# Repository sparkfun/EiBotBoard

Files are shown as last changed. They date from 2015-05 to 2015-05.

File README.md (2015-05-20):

EiBotBoard
==========
EiBotBoard

[*EiBotBoard (WIG-10025)*](https://www.sparkfun.com/products/10025)

The EiBotBoard (EBB) was originally designed for the Egg-Bot project. 
It is a small (2.2" x 2.2") two channel stepper motor driver board with USB microcontroller. 
It is based on the UBW board and supports all of the commands that the UBW does (for the most part), plus several extra, like stepper motor commands and RC servo output commands.

Repository Contents
-------------------
* **/Hardware** - All Eagle design files (.brd, .sch)
* **/Production** - Production panel files (.brd)

License Information
-------------------
Distributed as-is; no warranty is given.

_**Note:** This product is a collaboration with Brian Schmalz. A portion of each sales goes back to him for product support and continued development._

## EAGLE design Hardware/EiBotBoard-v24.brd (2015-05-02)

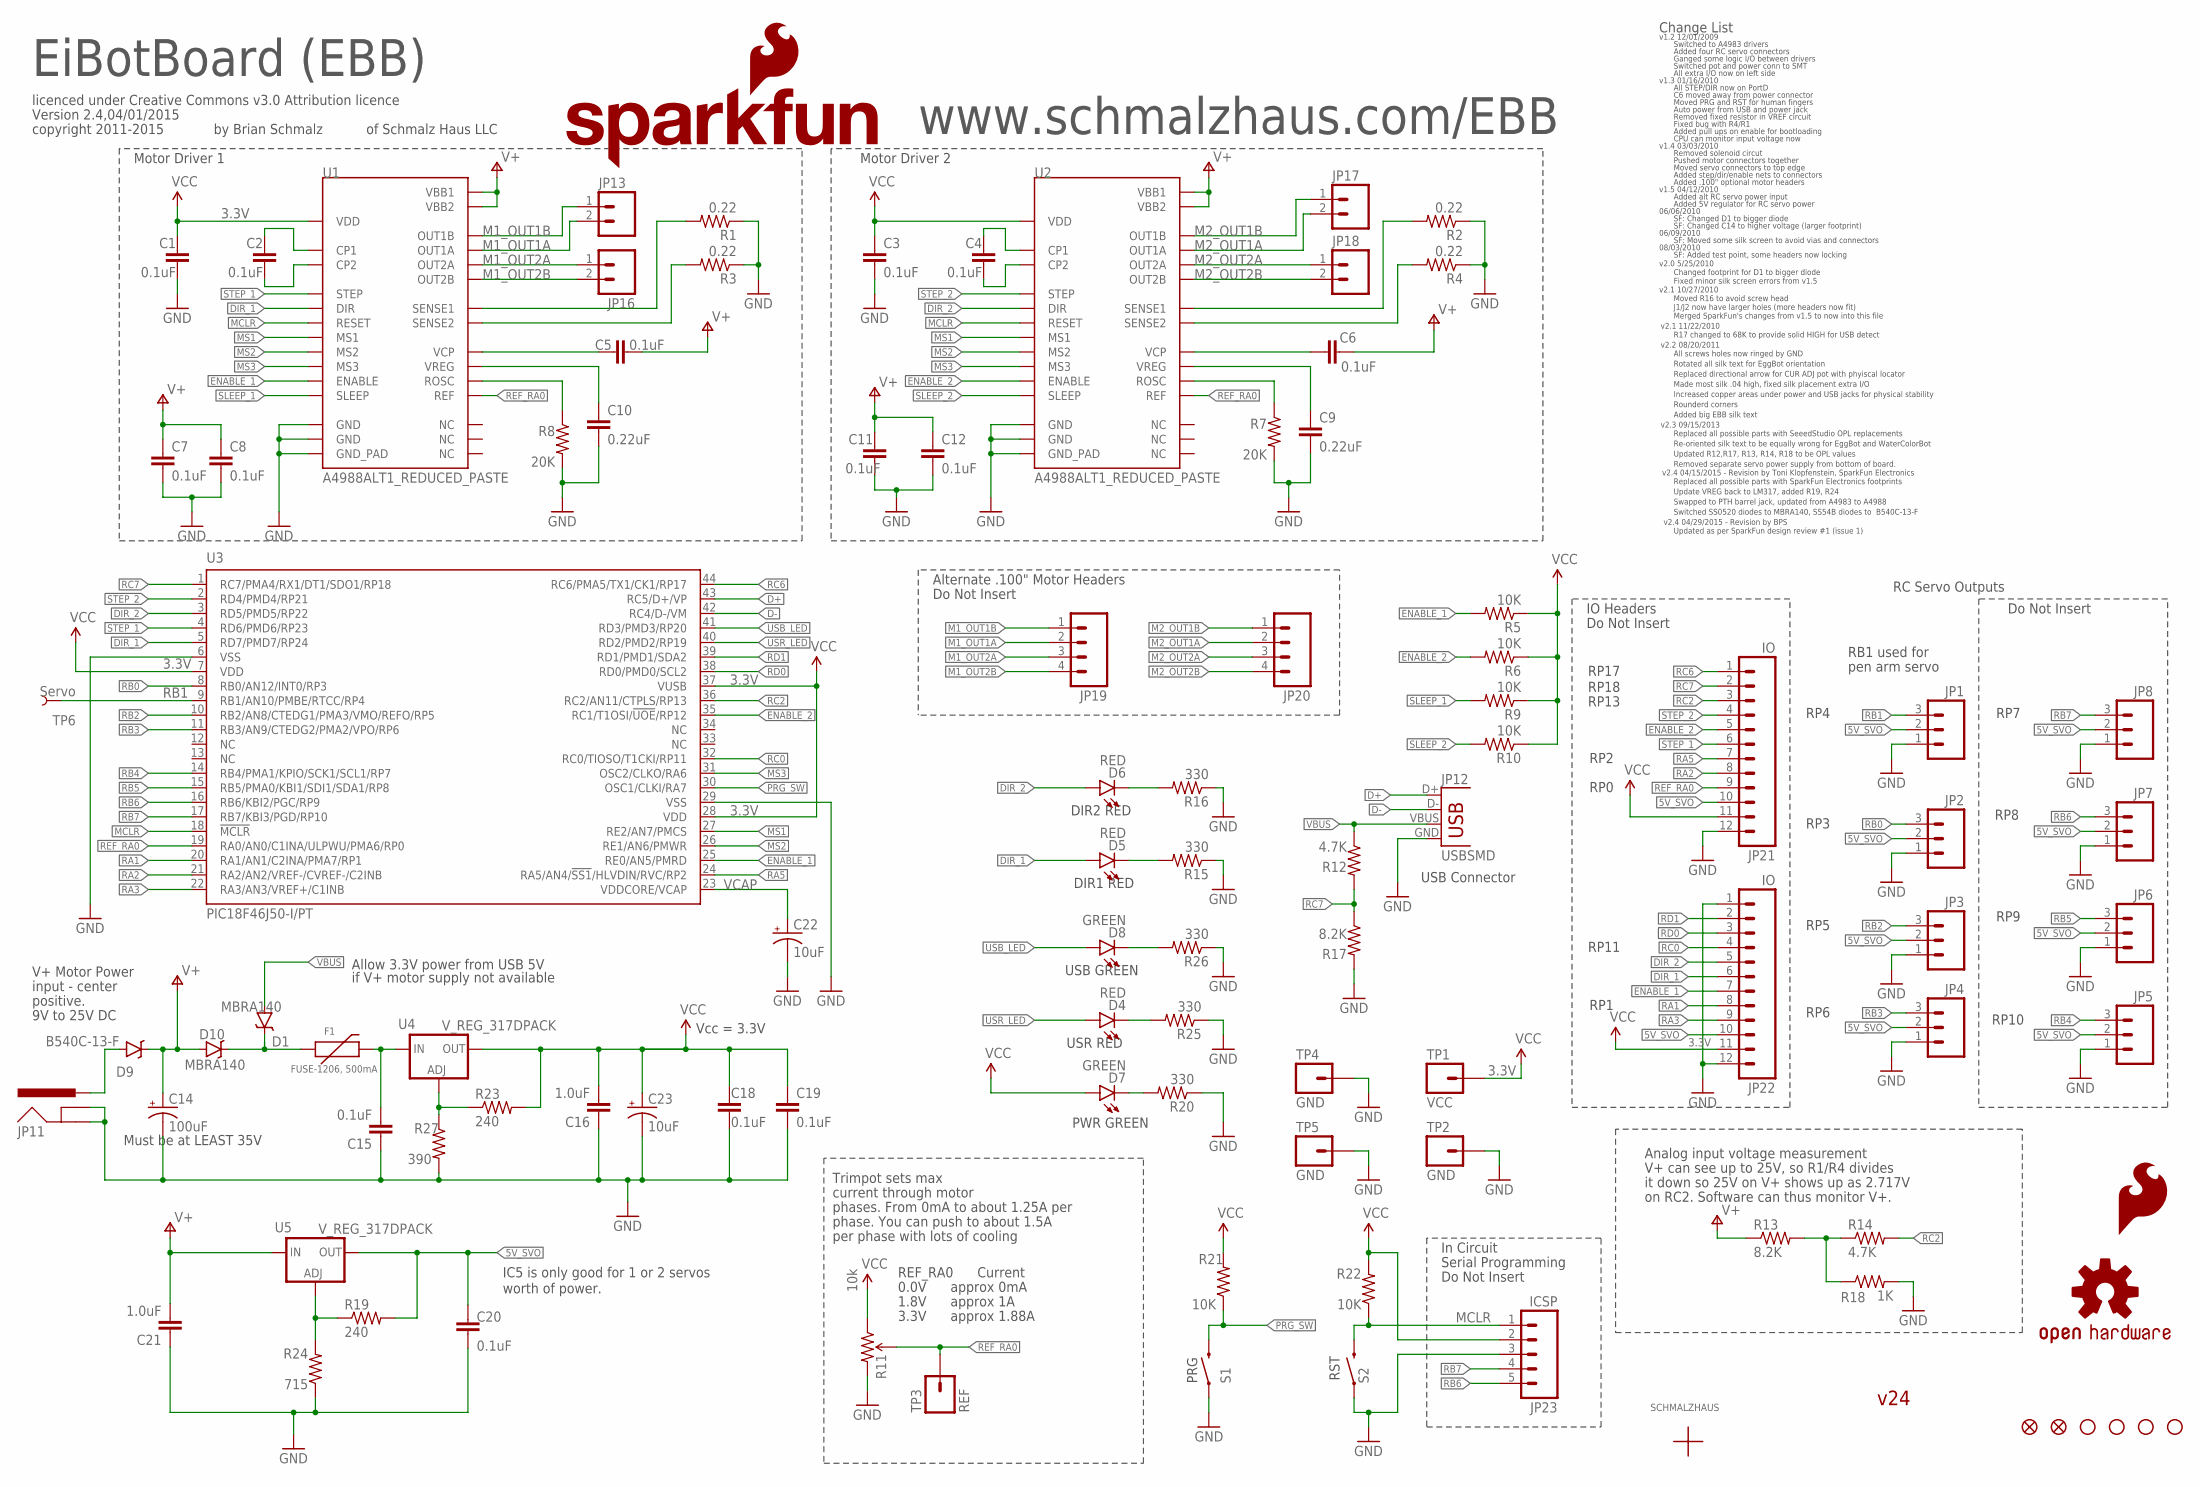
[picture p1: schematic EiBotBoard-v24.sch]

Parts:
C1, C2, C3, C4, C5, C6, C7, C8, C11, C12, C15, C18, C19, C20: 0.1uF; 0603-CAP
C9, C10: 0.22uF; 0603-CAP
C14: 100uF; NIC_10X10.5_CAP
C16, C21: 1.0uF; 0603-CAP
C22, C23: 10uF; EIA3528
D1, D10: MBRA140; SMA-DIODE
D4, D5, D6: RED; LED-0603
D7, D8: GREEN; LED-0603
D9: B540C-13-F; SMC
F1: FUSE-1206, 500mA; PTC-1206
JP1, JP2, JP3, JP4, JP5, JP6, JP7, JP8: M03LOCK_NO_SILK; 1X03_LOCK_NO_SILK
JP11: POWER_JACKPTH_LOCK; POWER_JACK_PTH_LOCK
JP12: USBSMD; USB-MINIB
JP13, JP16, JP17, JP18: M023.5MM_LOCK; SCREWTERMINAL-3.5MM-2_LOCK
JP14, JP15: FIDUCIAL1X2; FIDUCIAL-1X2
JP19, JP20: M04POLAR; MOLEX-1X4
JP21, JP22: IO; 1X12
JP23: ICSP; 1X05_NO_SILK
LOGO1: OSHW-LOGOS; OSHW-LOGO-S
LOGO2: SFE_LOGO_FLAME.2_INCH; SFE_LOGO_FLAME_.2
LOGO3: SFE_LOGO_NAME_FLAME.2_INCH; SFE_LOGO_NAME_FLAME_.2
R1, R2, R3, R4: 0.22; 0805
R5, R6, R9, R10, R21, R22: 10K; 0603-RES
R7, R8: 20K; 0603-RES
R11: 10k; TRIMPOT-3MM
R12, R14: 4.7K; 0603-RES
R13, R17: 8.2K; 0603-RES
R15, R16, R20, R25, R26: 330; 0603-RES
R18: 1K; 0603-RES
R19, R23: 240; 0603-RES
R24: 715; 0603-RES
R27: 390; 0603-RES
S1, S2: SWITCH-MOMENTARY-2SMD; TACTILE-SWITCH-SMD
TP1: VCC; 1X01_NOSILK
TP2, TP4, TP5: GND; 1X01_NOSILK
TP3: REF; 1X01
TP6: Servo; PAD.03X.05
U1, U2: A4988ALT1_REDUCED_PASTE; QFN-28-5MM_ALT1_REDUCED_PASTE
U3: PIC18F46J50-I/PT; TQFP44
U4, U5: V_REG_317DPACK; V-REG_DPACK
U$1: SCHMALZHAUSSCHMALZHAUS_SMALL; SCHMALZHAUS_SMALL
U$2, U$3, U$4, U$5: STAND-OFF

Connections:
3.3V: C1.1, C3.1, C16.2, C18.2, C19.2, C23.A (+), D7.A, JP21.11, JP22.11, JP23.2, R5.1, R6.1, R9.1, R10.1, R11.1 (CCW), R21.2, R22.2, R23.2, TP1.1, U1.P$15 (VDD), U2.P$15 (VDD), U3.7 (VDD), U3.28 (VDD), U3.37 (VUSB), U4.4 (OUT)
5V_SVO: C20.2, JP1.2, JP2.2, JP3.2, JP4.2, JP5.2, JP6.2, JP7.2, JP8.2, JP21.10, JP22.10, R19.2, U5.4 (OUT)
D+: JP12.D+, U3.43 (RC5/D+/VP)
D-: JP12.D-, U3.42 (RC4/D-/VM)
DIR_1: D5.A, JP22.6, U1.P$19 (DIR), U3.5 (RD7/PMD7/RP24)
DIR_2: D6.A, JP22.5, U2.P$19 (DIR), U3.3 (RD5/PMD5/RP22)
ENABLE_1: JP22.7, R5.2, U1.P$2 (ENABLE), U3.25 (RE0/AN5/PMRD)
ENABLE_2: JP21.5, R6.2, U2.P$2 (ENABLE), U3.35 (RC1/T1OSI/!UOE!/RP12)
GND: C1.2, C3.2, C7.2, C8.2, C9.2, C10.2, C11.2, C12.2, C14.-, C15.1, C16.1, C18.1, C19.1, C20.1, C21.1, C22.C (-), C23.C (-), JP1.1, JP2.1, JP3.1, JP4.1, JP5.1, JP6.1, JP7.1, JP8.1, JP11.GND, JP11.GNDBREAK, JP12.GND, JP21.12, JP22.1, JP22.12, JP23.3, R1.1, R2.1, R3.1, R4.1, R7.2, R8.2, R11.3 (CW), R15.1, R16.1, R17.2, R18.2, R20.1, R24.1, R25.1, R26.1, R27.2, S1.1, S2.1, TP2.1, TP4.1, TP5.1, U1.P$3 (GND), U1.P$18 (GND), U1.P$29 (GND_PAD), U2.P$3 (GND), U2.P$18 (GND), U2.P$29 (GND_PAD), U3.6 (VSS), U3.29 (VSS)
M1_OUT1A: JP13.2, JP19.2, U1.P$24 (OUT1A)
M1_OUT1B: JP13.1, JP19.1, U1.P$21 (OUT1B)
M1_OUT2A: JP16.1, JP19.3, U1.P$26 (OUT2A)
M1_OUT2B: JP16.2, JP19.4, U1.P$1 (OUT2B)
M2_OUT1A: JP17.2, JP20.2, U2.P$24 (OUT1A)
M2_OUT1B: JP17.1, JP20.1, U2.P$21 (OUT1B)
M2_OUT2A: JP18.1, JP20.3, U2.P$26 (OUT2A)
M2_OUT2B: JP18.2, JP20.4, U2.P$1 (OUT2B)
MCLR: JP23.1, R22.1, S2.3 (2), U1.P$12 (RESET), U2.P$12 (RESET), U3.18 (!MCLR!)
MS1: U1.P$9 (MS1), U2.P$9 (MS1), U3.27 (RE2/AN7/PMCS)
MS2: U1.P$10 (MS2), U2.P$10 (MS2), U3.26 (RE1/AN6/PMWR)
MS3: U1.P$11 (MS3), U2.P$11 (MS3), U3.31 (OSC2/CLKO/RA6)
unnamed: D6.C, R16.2
unnamed: D1.C, D10.C, F1.1
unnamed: C2.1, U1.P$4 (CP1)
unnamed: R13.2, R14.1, R18.1
unnamed: C2.2, U1.P$5 (CP2)
unnamed: D9.A, JP11.PWR
unnamed: D5.C, R15.2
unnamed: D8.C, R26.2
unnamed: R23.1, R27.1, U4.1 (ADJ)
unnamed: D4.C, R25.2
unnamed: D7.C, R20.2
unnamed: R19.1, R24.2, U5.1 (ADJ)
unnamed: C4.1, U2.P$4 (CP1)
unnamed: C4.2, U2.P$5 (CP2)
unnamed: R8.1, U1.P$13 (ROSC)
unnamed: C10.1, U1.P$8 (VREG)
unnamed: C5.1, U1.P$6 (VCP)
unnamed: R3.2, U1.P$27 (SENSE2)
unnamed: R1.2, U1.P$23 (SENSE1)
unnamed: C15.2, F1.2, U4.3 (IN)
unnamed: C6.1, U2.P$6 (VCP)
unnamed: R2.2, U2.P$23 (SENSE1)
unnamed: R4.2, U2.P$27 (SENSE2)
unnamed: C9.1, U2.P$8 (VREG)
unnamed: R7.1, U2.P$13 (ROSC)
PRG_SW: R21.1, S1.3 (2), U3.30 (OSC1/CLKI/RA7)
RA1: JP22.8, U3.20 (RA1/AN1/C2INA/PMA7/RP1)
RA2: JP21.8, U3.21 (RA2/AN2/VREF-/CVREF-/C2INB)
RA3: JP22.9, U3.22 (RA3/AN3/VREF+/C1INB)
RA5: JP21.7, U3.24 (RA5/AN4/!SS1!/HLVDIN/RVC/RP2)
RB0: JP2.3, U3.8 (RB0/AN12/INT0/RP3)
RB1: JP1.3, TP6.P$1, U3.9 (RB1/AN10/PMBE/RTCC/RP4)
RB2: JP3.3, U3.10 (RB2/AN8/CTEDG1/PMA3/VMO/REFO/RP5)
RB3: JP4.3, U3.11 (RB3/AN9/CTEDG2/PMA2/VPO/RP6)
RB4: JP5.3, U3.14 (RB4/PMA1/KPIO/SCK1/SCL1/RP7)
RB5: JP6.3, U3.15 (RB5/PMA0/KBI1/SDI1/SDA1/RP8)
RB6: JP7.3, JP23.5, U3.16 (RB6/KBI2/PGC/RP9)
RB7: JP8.3, JP23.4, U3.17 (RB7/KBI3/PGD/RP10)
RC0: JP22.4, U3.32 (RC0/TIOSO/T1CKI/RP11)
RC2: JP21.3, R14.2, U3.36 (RC2/AN11/CTPLS/RP13)
RC6: JP21.1, U3.44 (RC6/PMA5/TX1/CK1/RP17)
RC7: JP21.2, R12.2, R17.1, U3.1 (RC7/PMA4/RX1/DT1/SDO1/RP18)
RD0: JP22.3, U3.38 (RD0/PMD0/SCL2)
RD1: JP22.2, U3.39 (RD1/PMD1/SDA2)
REF_RA0: JP21.9, R11.2 (WIPER), TP3.1, U1.P$17 (REF), U2.P$17 (REF), U3.19 (RA0/AN0/C1INA/ULPWU/PMA6/RP0)
SLEEP_1: R9.2, U1.P$14 (SLEEP)
SLEEP_2: R10.2, U2.P$14 (SLEEP)
STEP_1: JP21.6, U1.P$16 (STEP), U3.4 (RD6/PMD6/RP23)
STEP_2: JP21.4, U2.P$16 (STEP), U3.2 (RD4/PMD4/RP21)
USB_LED: D8.A, U3.41 (RD3/PMD3/RP20)
USR_LED: D4.A, U3.40 (RD2/PMD2/RP19)
V+: C5.2, C6.2, C7.1, C8.1, C11.1, C12.1, C14.+, C21.2, D9.C, D10.A, R13.1, U1.P$22 (VBB1), U1.P$28 (VBB2), U2.P$22 (VBB1), U2.P$28 (VBB2), U5.3 (IN)
VBUS: D1.A, JP12.VBUS, R12.1
VCAP: C22.A (+), U3.23 (VDDCORE/VCAP)

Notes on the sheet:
EiBotBoard (EBB)
v1.2 12/01/2009
by Brian Schmalz
of Schmalz Haus LLC
www.schmalzhaus.com/EBB
licenced under Creative Commons v3.0 Attribution licence
PWR GREEN
DIR1 RED
DIR2 RED
USR RED
USB GREEN
PRG
RST
RP17
RP18
Change List
Switched to A4983 drivers
Added four RC servo connectors
Ganged some logic I/O between drivers
Switched pot and power conn to SMT
All extra I/O now on left side
Vcc = 3.3V
v1.3 01/16/2010
All STEP/DIR now on PortD
C6 moved away from power connector
Moved PRG and RST for human fingers
Auto power from USB and power jack
Removed fixed resistor in VREF circuit
Fixed bug with R4/R1
CPU can monitor input voltage now
Added pull ups on enable for bootloading
V+ can see up to 25V, so R1/R4 divides
it down so 25V on V+ shows up as 2.717V
Analog input voltage measurement
on RC2. Software can thus monitor V+.
RP11
Version 2.4,04/01/2015
v1.4 03/03/2010
Removed solenoid circut
Pushed motor connectors together

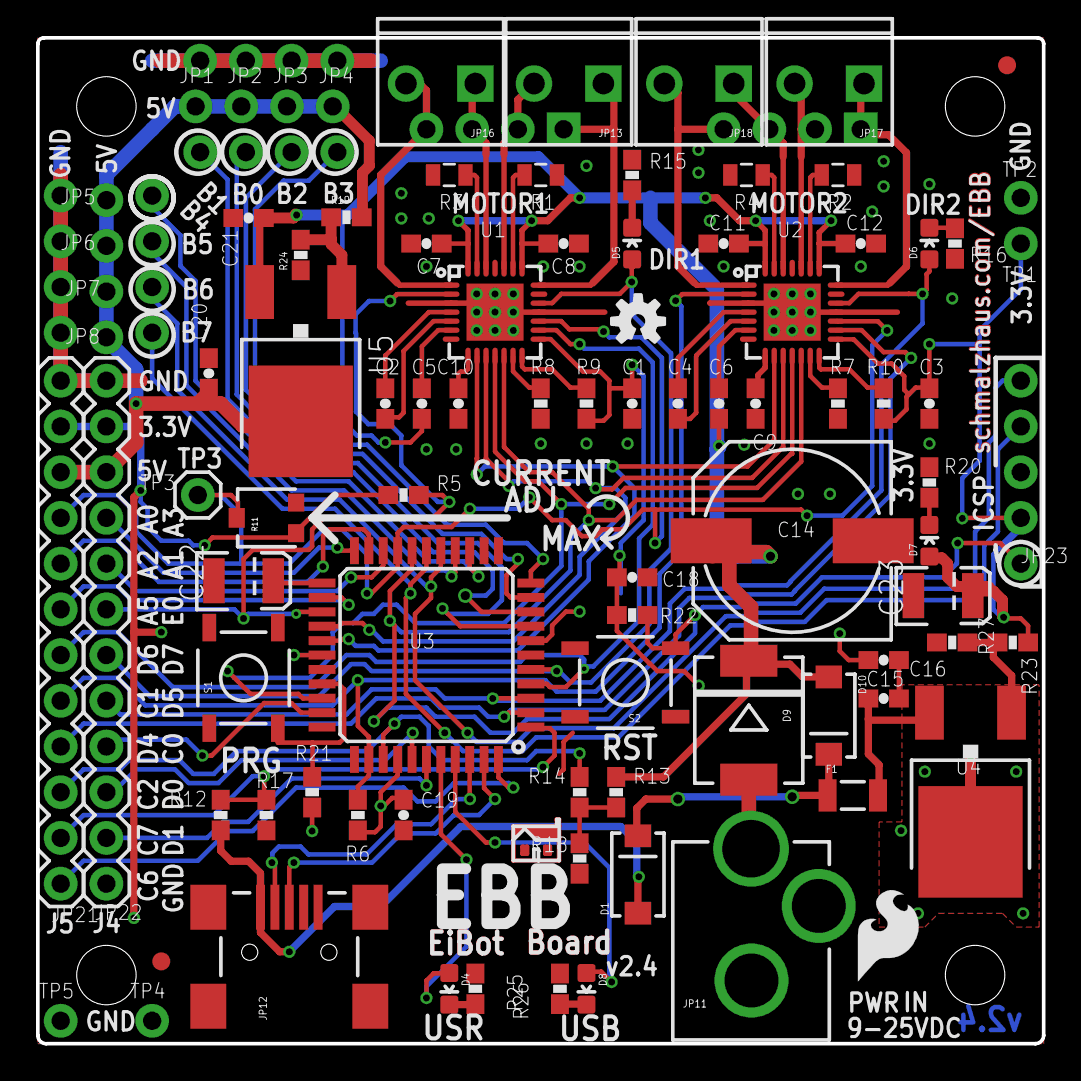
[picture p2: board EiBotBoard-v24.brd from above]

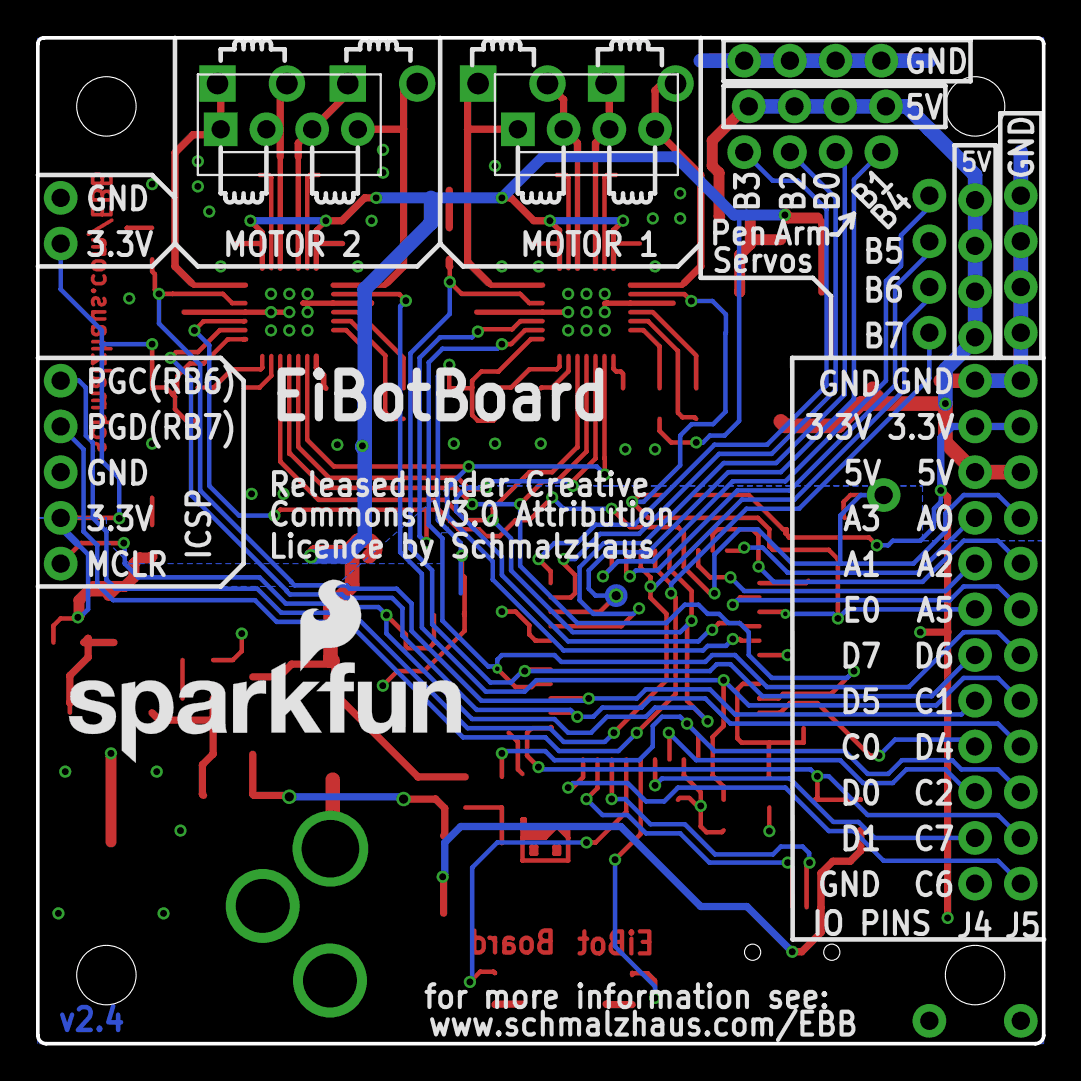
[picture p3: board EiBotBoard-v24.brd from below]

Board: 2 copper layers, 55.9 x 55.9 mm, 99 parts (4 on the bottom side), 75 nets.

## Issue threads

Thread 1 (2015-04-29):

design review v2.4

lewispg228, 2015-04-29:
Nice work on this! After running the checklist, I found some minor things. Here is my summary/issues:

1) Does the frame have the proper CC attribution? (Frame- Letter/Ledger, CC 4.0) [NO]
comment: exception for v3.0 and old frame

2) Are there any 4-way junctions? [YES]
comment: right side of IC4

3) Are dashed grey lines ('info' eagle layer 97) used to clearly separate different areas? [NO]
comment: If Brian S. really wants it to stay on "guide" layer I suppose it could, but standard layer is "info"

4) Does every part have a NAME and VALUE (with proper prefix and no '$')? [NO]
comment: ICs should be U1, U2, U3

5) Is the LED color standard followed? (red for power, blue for STAT, green for TX, yellow for RX) [NO]
comment: The User LED is kindof a stat, so shouldn't it be blue?

6) Is trace routing up to spec? (to/from center-points, straight lines, 45 angles, 'T' intersections, no right angles or acid traps) [NO]
comment: acid trap coming off left pad of trimpot

7) Are all QFN components with 6 or more leads 75 percent pasted? [NO]
comment: Just talked to Bob and concurred that we should move to a paste comparable to ioio TPS chip, please use A4983ALT1_REDUCED_PASTE

8) Is there a correct version number in the copper? [NO]
comment: Not sure if it's an issue, but your revision note says 4/25/2015, and copper says 4/1/2015, also do we want to go with v24 in copper?

9) Are the board dimensions on 0.05 inch or 0.01 inch grid? [NO]
comment: I guess it's fine that this be slightly off the .05 inch grid, but bottom left should still be set to 0,0

10) Is the SparkFun Logo on the board? [YES]
comment: bottom side logo currently getting chopped a bit by barrel jack

11*) I was wondering if it was discussed with Brian S. about populating the remaining servo connectors with male 0.1 headers?

12*) Any more thoughts on adding silk to show min/max on the current trim pot?

EmbeddedMan, 2015-04-29:
Pete,

Thanks - all great comments. I'll address them one by one:

1) I do not want to release this as CC 4.0. I ask that SparkFun respect my
wishes and not change the licence on my board. Thanks for granting me an
exception.

2) I was not aware that 4-way junctions are bad ideas. What's the reason
these are to be avoided?

3) Oops. My bad. You are quite correct - info is better than guide. I will
correct and push an update.

4) Good catch. I'll update this as well.

5) The EBB has always had red/green LEDs. Changing colors now is not a good
idea because it invalidates any existing documentation for this product. If
we were just starting this design, I'd be OK with going blue.

6) From the research I've been able to do, acid traps are something that
mattered years ago when etching processes were not as well controlled as
they are today. I'm not aware of any reason why this is a bad idea today -
if you know otherwise, please point me in the direction of the research
that shows this. (Our PCB layout guys at Logic PD - very experienced and
well respected - taught me this about acid traps.)

7) Not being familiar enough with your process, I don't have a comment on
this one. You need to do what you need to do to make it reflow properly.

8) I've had several back and forth e-mails with various SparkFun employees
over the years about version numbers. I always argued for putting a version
number on the board somewhere, and I was told you guys don't like putting
version numbers on the board. I put them on the EBB silk because I felt
they were a good idea. I'm fine with having a version number somewhere on
the board, and in a copper layer is fine by me as long as it is also on the
silk. I will change the copper text to be the same as the silk text, and
all should be 2.4 I believe. Let me know if this isn't a good resolution to
your issue.

9) Cool. Not a problem. - I will update the board to be 2.20" x 2.20" and
then the lower left will be at 0,0.

10) I don't see how the bottom Sparkfun logo could be obscured by the
barrel jack - the barrel jack is on the top side of the board, and none of
the logo overlaps with the barrel jack holes. If you'd like it moved, I
don't mind at all - I'm just not quite sure how to resolve this issue.
Maybe you mean the SparkFun logo on the top side? I can nudge that guy a
bit.

11) Honestly, I'd rather have all 8 RC servo connections populated. Even
better would be to have all I/O (J5 and J5) populated with male headers
sticking up. That way nobody would have to solder connectors in to use any
of those features.

12) Frankly I gave up on trying to accurately portray MIN/MAX on the silk,
because the pot part got changed several times (without revving the board)
on the Easy Driver, and each time the pot was in the opposite direction as
the silk. So users were confused for a significant portion of the Easy
Driver's life. If you can commit to using only pots that respect the
MIN/MAX direction that we put on the silk, I'd be really happy to add it
back in to EBB (And Easy Driver and Big Easy Driver).  But having no silk
is better than having it wrong, I've found, from a support perspective. (I
always just tell people to get their DMM out and monitor the voltage at TP3
anyway.)

*Brian

On Wed, Apr 29, 2015 at 3:16 PM, Pete Lewis <notifications@github.com>
wrote:

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

lewispg228, 2015-04-29:
Hi Brian,
Thanks for your quick and thorough response!

2) 4-ways leave the opportunity for a net to be drawn "underneath" the node (allowing for two separate net lines to "look" connected). Although this same problem can occur with 3-ways, it is less likely that a designer would draw in an "accidental" node. In fact, we discourage any designer to use the node tool, and only allow nodes to form (automatically) when you intentionally connect two net wires.

5) okay

6) Thanks for your input. I will bring this up at the next engineering meeting, and maybe we will no longer require avoiding acid traps.

8) Please keep version in top silk and change "date code" in bottom copper to "v24" (Date codes usually indicate super old pcb designs, and could cause some confusion)

10) The Bstop of the barrel jack pad is just barely cutting into the "a" of the sparkfun logo. might as well nudge it up a bit to clear the bstop.

11) Thanks for your input. We will look into the cost increase and let you know about any potential price increase.

On the topic of PTH population, it is also worth mentioning that we are going to shift this onto our selective solder machine and so the headers JP19 and JP20 will be filled in with solder (as is). If you need them to remain open, then they will need to be scooted downward and away from the screw terminal pads at least 0.02 inch. (This is so the fountain of solder can access the screw terminal pads without also filling in the nearby pads)

12) We will commit to using the correct part. Silk will be helpful for our techs during production testing too.

EmbeddedMan, 2015-04-29:
Pete,

Fantastic.

2) Oh, you meant in the SCHEMATIC! Of course. Those are super bad. I try to
always check for those. Thanks for catching this one. I'll fix it right
away.

8) Cool, will do. Bottom copper will get v24, as will top silk.

10) Ahh, I see the problem now. I was looking at the version-v23 branch,
not the version-v24 branch. I'm now looking at the same files you are.
Sorry! Yup, I can fix that problem.

As for JP19 and JP20, I think it's fine that they're filled with solder. I
don't mind that at all. Will that cause a problem for you when you program
the CPU?
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
EmbeddedMan, 2015-04-30:
Toni/Pete,

I'm fine making the changes (wider dimension line, removing outline on
tplace, and updating the two driver chips). I'll take care of them when I
get home from work tonight.

Pete-

Yes, you have the LED colors correct. Thanks-

*Brian

On Thu, Apr 30, 2015 at 12:38 PM, Toni Klopfenstein <
notifications@github.com> wrote:

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

lewispg228, 2015-04-30:
Thanks Brian. That sounds good.

Also, we are cool with making an exception about the LED colors. Please swap them back when you work on the design tonight, and please ensure to use the following two parts in the SparkFun-LED library:

LED-RED0603 (LED-RED) - note the attribue PROD_ID DIO-00819
LED-GREEN0603 (LED-GREEN) - note the attribue PROD_ID DIO-00821

EmbeddedMan, 2015-04-30:
Quick find on acid traps:
http://electronics.stackexchange.com/questions/115653/are-acid-traps-real-2014

Summary: acid traps may possibly still be an issue if you're using really
really cheap Chinese board vendors. Some US board houses still flag them as
errors however.

*Brian

On Thu, Apr 30, 2015 at 2:59 PM, Pete Lewis <notifications@github.com>
wrote:

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

EmbeddedMan, 2015-05-01:
OK, all changes as specified above have been made and pushed to GitHub.
Give it a quick check to make sure I didn't forget anything, and then I
think we're good to go except for the pot issue.

*Brian

On Thu, Apr 30, 2015 at 4:54 PM, Brian Schmalz <brian@schmalzhaus.com>
wrote:

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

lewispg228, 2015-05-01:
Hi Brian,
Here is the info on the trimpot. I have confirmed with our purchasing that we will continue to only buy this exact part from Future. And if we ever need to get a substitute supplier or part, then it will go through our standard substitute verification (which will also involve you, as this is a collaboration).

BI Technologies, manufacturer # 22AR10KLFTR

http://www.futureelectronics.com/en/technologies/passives/resistors/variable-resistors/Pages/7624471-22AR10KLFTR.aspx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

http://www.bitechnologies.com/pdfs/22.pdf

Please update the silk to indicate MIN/MAX. Then I will verify all changes, and we'll get some protos on order!

PS. Thanks for the links about acid traps. It's good to read some other peoples experience. I will definitely forward it on to our engineering group. Although our fab house (in China) does good work, I would not say they are the best available. In fact, they are the cheapest we can find. We notice a lot of "X"'d out boards (usually in the 1-2% range). Although this is good that they catch any boards with errors during electrical flying probe testing, it's wasteful. Not only with the materials we have to throw in the E-waste, but also our time pasting additional panels to meet our build quantities. I don't know if the X'd out boards were caused by acid traps, cold joints, accidental jumpers, or just fabrication mistakes, but anything we can do to minimize this, I'm all for.

I like the user, Daniel's, answer about spending 10 minutes at the end of a layout to clean them up, or even better, avoid making them while doing the layout. Being in the QC world, I always think 10 more minutes on a design is worth it - even to avoid a sub-1% error in production, but that's why I'm in QC I suppose :)

EmbeddedMan, 2015-05-02:
Pete/Toni,

OK, current adjust max direction is now indicated on top silk layer.

Let me know if there is anything else you'd like done!

Thanks-
*Brian

On Fri, May 1, 2015 at 10:31 AM, Pete Lewis <notifications@github.com>
wrote:

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

lewispg228, 2015-05-20:
Hey Brian, Sorry for the delay in my response here. I just had my first kid on 5/3, and I'm just now getting back into the office. Little Graham came two weeks early, so I was a little flustered and didn't finish up this review.

Your latest commit looks good. We'll move forward with prototype of v24. Thanks for all your work on this Brian. This rev is going to be a great improvement!

@ToniCorinne, can you please get the BOM and Assembly sheet updated to include the necessary headers to populate all 8 RC servo connections and all I/O (J5 and J5) populated with male headers sticking up

ToniCorinne, 2015-05-20:
Assembly has been updated and these are officially out for protos.

EmbeddedMan, 2015-05-20:
Yes! Thanks so much to both of you - I'm really excited for this updated
EBB version.

*Brian

On Wed, May 20, 2015 at 6:05 PM, Toni Klopfenstein <notifications@github.com
> wrote:

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

Closed 2015-05-20.

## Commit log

2015-03-10 Adding hardware files, updating README
    [EiBotBoard-v23.brd, EiBotBoard-v23.sch]
2015-03-31 Version 2.3 from Schmalz Haus. This is the latest version that is in production at SeeedStudios (EMSL) and is shipping with EggBot and WatercolorBot. See changes.txt and schematic for list of changes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
    [EiBotBoard-v23.brd, EiBotBoard-v23.sch, EiBotBoard_v23_BOM.xls]
2015-04-02 Updating part numbers to SFE libraries, swapping vregs
    [EiBotBoard-v23.brd, EiBotBoard-v23.sch]
2015-04-03 Updating to A4988 ICs
    [EiBotBoard-v23.brd, EiBotBoard-v23.sch]
2015-04-03 Updating additional packages, fixing DRC errors
    [EiBotBoard-v23.brd, EiBotBoard-v23.sch]
2015-04-03 Adding dimension measures, license info and designer names to brd files
    [EiBotBoard-v23.brd]
2015-04-17 Updating to version 2.4
    [EiBotBoard-v24.brd, EiBotBoard-v24.sch]
2015-04-17 Removing v_23 files
    [EiBotBoard-v23.brd, EiBotBoard-v23.sch, EiBotBoard_v23_BOM.xls]
2015-04-30 Updated board and schematic as per Peter Lewis' design review nodes (issue #1 in GitHub)
    [EiBotBoard-v24.brd, EiBotBoard-v24.sch]
2015-05-01 Reverted LEDs back to their original colors, removed outline line on tPlace, made outline on dimension layer 0.008" wide, switched driver chip footprints to A4988ALT1_REDUCED_PASTE.
    [EiBotBoard-v24.brd, EiBotBoard-v24.sch]
2015-05-02 Added MAX direction indication on top silk for current adjust pot.
    [EiBotBoard-v24.brd, EiBotBoard-v24.sch]
2015-05-20 Pushing BOM update

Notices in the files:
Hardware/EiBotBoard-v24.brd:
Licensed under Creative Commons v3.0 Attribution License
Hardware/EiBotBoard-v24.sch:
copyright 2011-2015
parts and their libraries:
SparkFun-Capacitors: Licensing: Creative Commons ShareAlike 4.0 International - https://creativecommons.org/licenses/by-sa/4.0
